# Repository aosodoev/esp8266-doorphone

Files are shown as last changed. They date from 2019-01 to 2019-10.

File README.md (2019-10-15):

# ESP8266 door phone w/ RFID lock

> If it looks stupid but works, it ain't stupid.

Crude door phone and RFID lock project for my yard gates door.

Handset unit serves as WiFi gateway/extender creating soft AP for door unit and connecting to existing WiFi network and MQTT broker.

Basic keys management and lock control via home assistant.

Using [PlatformIO](https://platformio.org) environment for development.

## Configuration
Create AP_credentials.h file in src dir (see doorphone.h for definitions). 

Edit mqtt_server param (without .local suffix) in settings.txt.

MQTT brocker IP address resolved via ESP8266mDNS library and requires MQTT service to be advertised.

e.g. mosquitto avahi service config: 

/etc/avahi/services/mosquitto.service
```
<!DOCTYPE service-group SYSTEM "avahi-service.dtd">
<service-group>
 <name replace-wildcards="yes">Mosquitto on %h</name>
  <service>
   <type>_mqtt._tcp</type>
   <port>1883</port>
   <txt-record>More info at mqtt.org</txt-record>
  </service>
</service-group>
```

## Hardware

As this is one time build, it's based on breakout boards/modules from ebay/aliexpress soldered to a perfboard.

Power door lock actuator unlocks a simple door bolt. Reed switch and a magnet used as door contact switch.

Initially it was very simple lock controller with one "open" button. Door phone and RFID reader were added later.

Audio quality turned out to be pretty good. There is no feedback noise due to earphone on the handset side. To get rid of digital noise and echo use shielded cable for microphone signal.

### Breakout boards/modules

MFRC522 reader missing here, any RC522 with SPI interface should work.

MCP3021 or TLC549 ADC can be used, add "ADC8BIT" define to build flags in case of TLC549 (see platformio.ini).

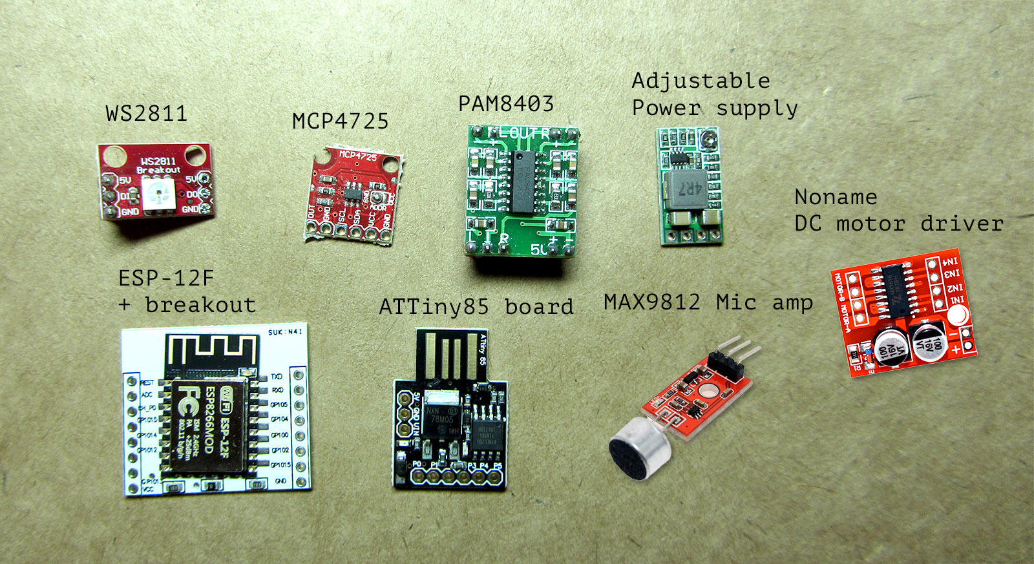
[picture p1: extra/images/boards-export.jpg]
Breakout boards


### Schematics

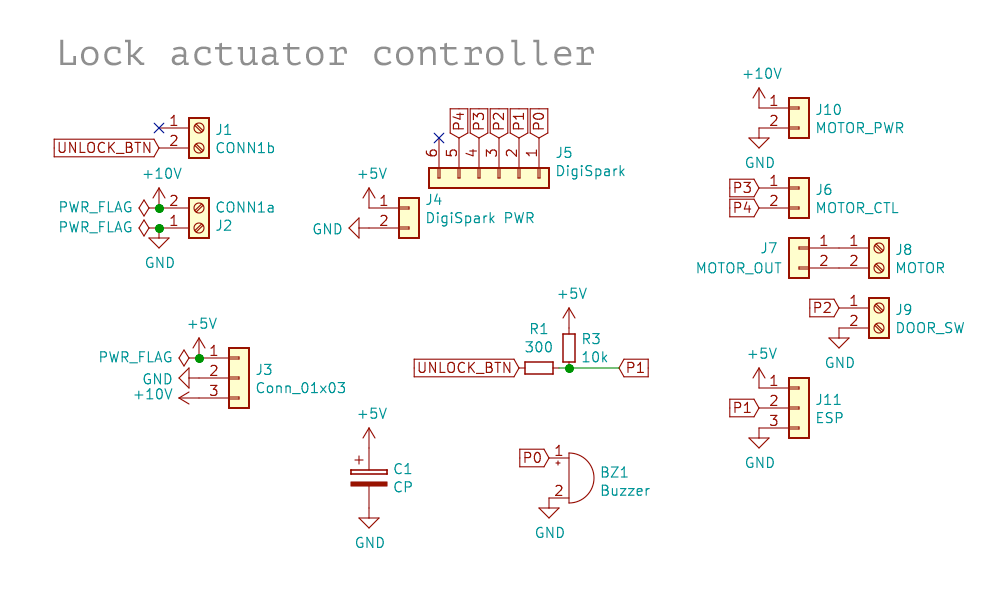
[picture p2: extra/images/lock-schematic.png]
Lock controller schematic


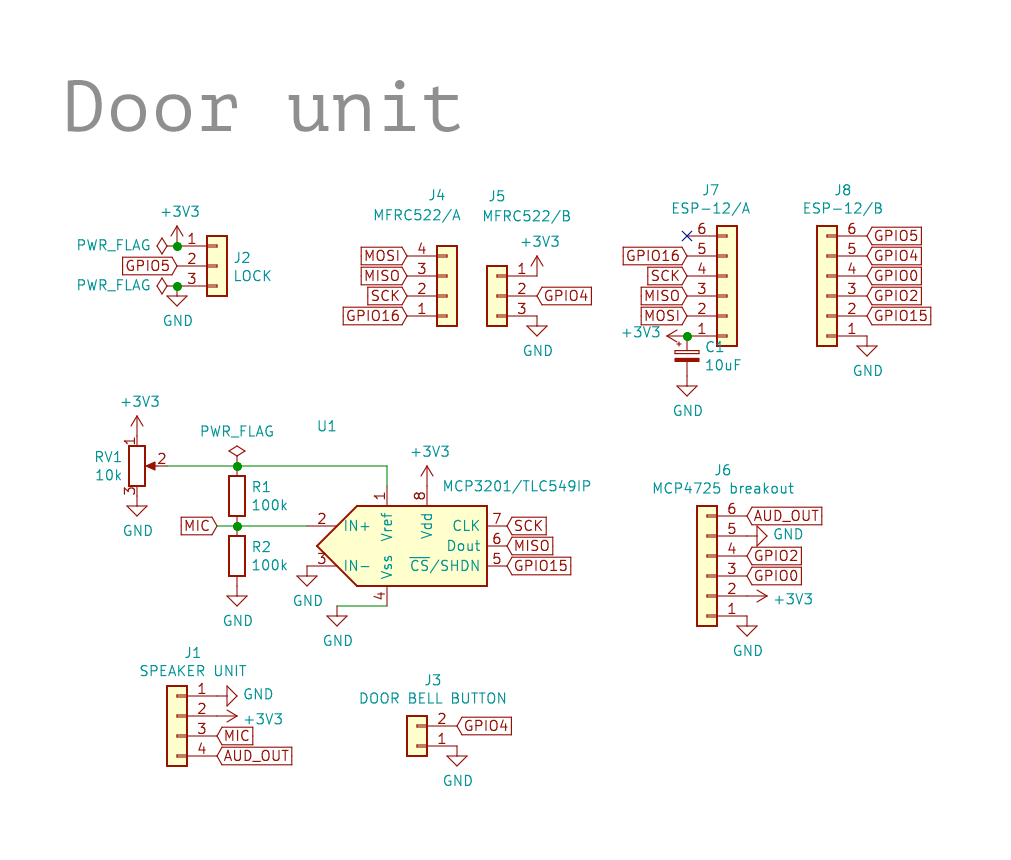
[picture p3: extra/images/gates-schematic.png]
Door unit schematic


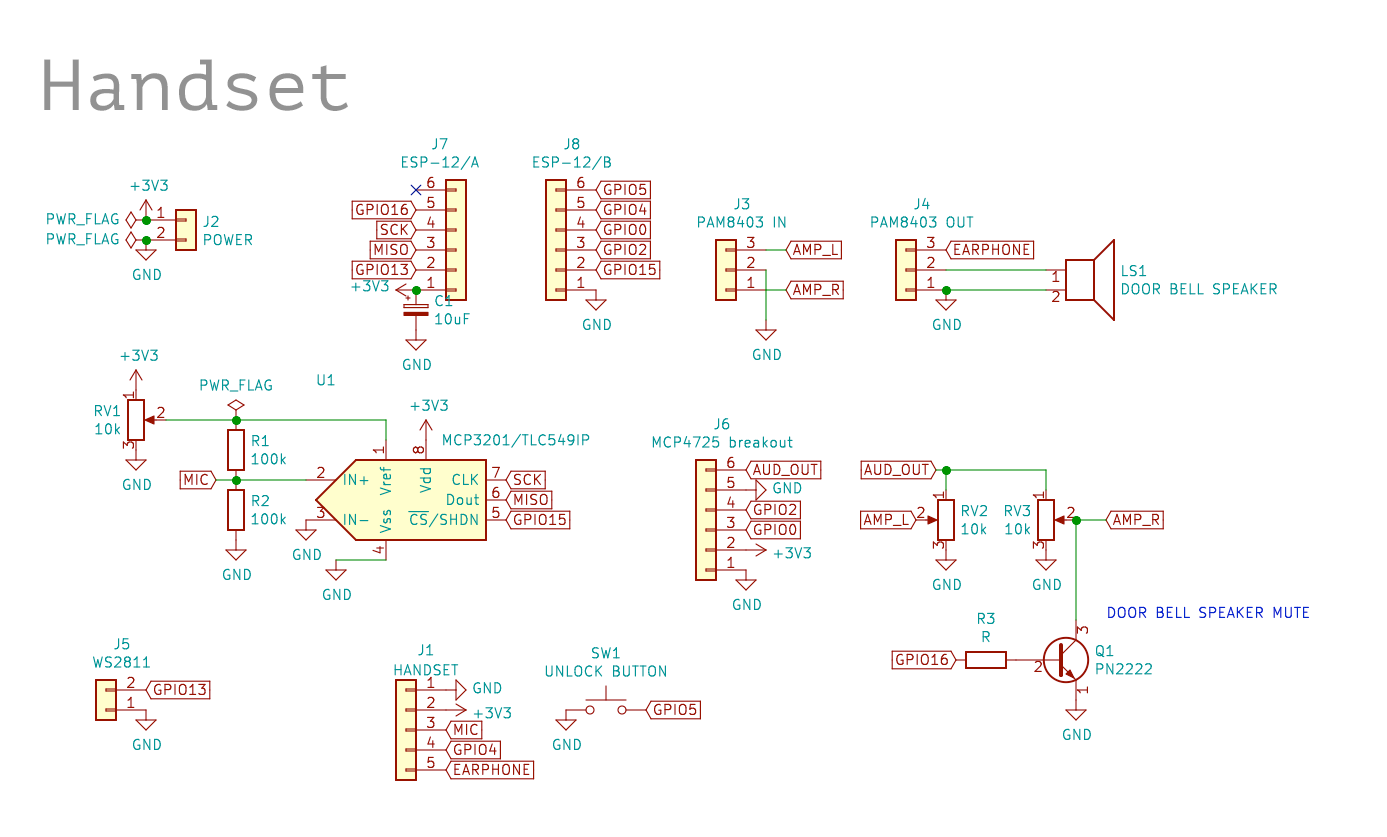
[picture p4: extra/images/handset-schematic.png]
Handset unit schematic


# WARNING
This implementation of RFID access control isn't even remotely secure and should not be used in any critical situation!

## Audio sources from freesound.org:

- Success: [https://freesound.org/people/grunz/sounds/109662/](https://freesound.org/people/grunz/sounds/109662/)

- Error: [https://freesound.org/people/Breviceps/sounds/445978/](https://freesound.org/people/Breviceps/sounds/445978/)

- "Door bell": [https://freesound.org/people/pac007/sounds/331567/](https://freesound.org/people/pac007/sounds/331567/)

- "Chirp": [https://freesound.org/people/IFartInUrGeneralDirection/sounds/96195/](https://freesound.org/people/IFartInUrGeneralDirection/sounds/96195/)

- "Electronic chirp": [https://freesound.org/people/organicmanpl/sounds/386973/](https://freesound.org/people/organicmanpl/sounds/386973/)

- "Echo": [https://freesound.org/people/Thoribass/sounds/254819/](https://freesound.org/people/Thoribass/sounds/254819/)

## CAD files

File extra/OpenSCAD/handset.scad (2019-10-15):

include<fillets.scad>
include<MCAD/units.scad>
use<MCAD/boxes.scad>
use<scad-utils/morphology.scad>
use<scad-utils/mirror.scad>

e = epsilon;
fitting_tolerance = 0.2;
boards_tolerance = 0.2;

shell_thickness = 1.6;
front_panel_thickness = 2;
inner_width = 46;
inner_height = 150;
inner_depth = 15;
inner_radius = 3;
outer_back_radius = 7.6;
front_cover_brim_depth = 4;

esp_board_width = 32;
esp_board_height = 28;
esp_board_thickness = 5.6;

speaker_radius = 14.9/2;
speaker_brim_height = 2.2;

mic_board_height = 14.1;
mic_radius = 9.6/2;
mic_height = 6.5;

ringtone_amp_height = 17.3;
ringtone_amp_width = 25.1;

outer_width = inner_width + 2*(shell_thickness + fitting_tolerance);
outer_height = inner_height + 2*(shell_thickness + fitting_tolerance);
outer_depth = inner_depth + front_panel_thickness + 2*shell_thickness;
outer_radius = inner_radius + shell_thickness + fitting_tolerance;


view = "explode";

if (view == "explode") {
     translate([0, 0, outer_depth - front_panel_thickness + 20]) {
	  rotate([0, 180, 0]) {
	       front_cover();
	  }
     }
     translate([0, 0, outer_depth - front_panel_thickness + 40]) {
	  %color([0.5, 0.5, 0.8, 0.5]) {
	       front_panel();
	  }
     }
     %color([0.5, 0.8, 0.5, 0.5]) {
	  back_cover();
     }
} else if (view == "handset-front-cover") {
     front_cover();
} else if (view == "handset-back-cover") {
     back_cover();
} else if (view == "handset-front-panel") {
     front_panel();
} else if (view == "handset-stand") {
     stand();
}

* union() {

    // test mic mount
    * test([20, 14, outer_height], 2) {
        front_cover();
    }

    // test speaker mount
    *test([20, 20, 7], inner_height - inner_width/2 - 10) {
        front_cover();
    }

    // test usb and reed switch
    * test([20, 26, 10], -3) {
        back_cover();
    }


    * test([inner_width, inner_width - 2, inner_depth], 90 - inner_width/2) {
	 back_cover();
    }

    // test button 
    * union() {
        button(negative = "top");
        test([30, 35, outer_height], inner_height/2 - 28) { front_cover(); }
    }
}


function x(v) = v[0]; function y(v) = v[1]; function z(v) = v[2];

module stand() {
     stand_size = [outer_width + 2*14, 80, 50];
     handset_angle = 12;
     handset_offset = y(stand_size) - outer_depth - 8;
     cutout_width = outer_width + 4;
     cutout_height = outer_depth + 1 + 4;

     difference() {
	  intersection() {
	       linear_extrude(z(stand_size)) {
		    rounding(10, $fn = 64) {
			 square(stand_size + [0, y(stand_size)], center = true);			 
		    }
	       }
	       rotate([0, -90, 0]) {
		    linear_extrude(x(stand_size) + 2*e, center = true) {
			 polygon([
				      [0, 0],
				      [z(stand_size), 0],
				      [15, y(stand_size)],
				      [0, y(stand_size)]

					   ]);
		    }
	       }
	  }

	  translate([0, handset_offset, 0]) {
	       rotate([handset_angle, 0, 0]) {
		    translate([0, 0, 3/cos(handset_angle)]) {
			 linear_extrude(outer_height) {
			      intersection() {
				   translate([0, cutout_height]) {
					rounding(outer_back_radius + 1, $fn = 32) {
					     square([cutout_width, cutout_height*2], center = true);
					}
				   }
				   square([cutout_width, cutout_height*2], center = true);
			      }
			 }
		    }
	       }
	  }

	  translate([0, -e, -e]) {
	       intersection() {
		    rotate([-90 - 20, 0, 0]) {
			 linear_extrude(y(stand_size)*2, center = true) {
			      rounding(20-e, $fn = 64) {
				   square([40, 2*z(stand_size) - 15], center = true);
			      }
			 }
		    }
		    rotate([0, -90, 0]) {
			 linear_extrude(x(stand_size), center = true) {
			      polygon([
					   [0, 0],
					   [z(stand_size), 0],
					   [z(stand_size), handset_offset - 1.6/cos(handset_angle) - z(stand_size)*tan(handset_angle)],
					   [0, handset_offset - 2]
					   
					   ]);
			 }
		    }
	       }
	  }
	  translate([0, y(stand_size), -e]) {
	       linear_extrude(z(stand_size)) {
		    rounding(6, $fn = 16) {
			 square([cutout_width - 6*2, (y(stand_size) - handset_offset - 6) * 2], center = true);
		    }
	       }
	  }
	  mirror_x() {
	       rotate([-90, 0, 0]) {
		    translate([(x(stand_size) + 40)/4, -z(stand_size) + 18, -e]) {
			 translate([-6, -14, 3]) {
			      cube([12, 20, 4]);
			 }
			 cylinder(4, r = 4);
			 hull() {
			      cylinder(4, r = 2);
			      translate([0, -8, 0]) {
				   cylinder(4, r = 2);
			      }
			 }
		    }
	       }
	  }
     }

     reed_switch_position = 15 + 2 + shell_thickness;
     magnet_radius = 14.6/2;
     magnet_height = 3;

     translate([0, handset_offset - 1.6/cos(handset_angle), 0]) {
	  rotate([handset_angle, 0, 0]) {
	       translate([0, 0, reed_switch_position + 3/cos(handset_angle)]) {
		    rotate([90, 0, 0]) {
			 difference() {
			      hull() {
				   cylinder(6, r = magnet_radius + fitting_tolerance + 2);
				   translate([0, -6*1.2, 0]) {
					cylinder(e, r = magnet_radius + fitting_tolerance + 2);
				   }
			      }
			      difference() {
				   cylinder(6 + e, r = magnet_radius + fitting_tolerance, $fn = 64);
				   mirror_x(){
					mirror_y() {
					     translate([(magnet_radius + fitting_tolerance)*cos(45), (magnet_radius + fitting_tolerance)*cos(45), magnet_height + 0.4]) {
						  sphere(0.4, $fn = 64);
					     }
					}
				   }					
			      }
			 }
		    }
	       }
	  }
     }

     	  *translate([0, handset_offset, 0]) {
	       rotate([handset_angle, 0, 0]) {
		    translate([0, 0, 3/cos(handset_angle)]) {
			 color([0, 1, 0, 0.3]) {
			      linear_extrude(outer_height) {
				   intersection() {
					translate([0, outer_depth + 1]) {
					     rounding(outer_back_radius, $fn = 32) {
						  square([outer_width, outer_depth*2 + 1], center = true);
					     }
					}
					square([outer_width, outer_depth*2 + 1], center = true);
				   }
			      }
			 }
		    }
	       }
	  }

     
}
    
module front_panel() {

     front_panel_thickness = front_panel_thickness + 1;
     
     difference() {
	  union() {
	       translate([0, inner_height/2, 0]) {
		    linear_extrude(front_panel_thickness) {
                        rounding(r = inner_radius, $fn = 32) {
                            square([inner_width, inner_height], center = true);
                        }
                    }
	       }
	       front_panel_latches(negative = false);

	       translate([0, inner_height - inner_width/2 - fitting_tolerance, 0]) {
		    /* speaker(); */
	       }
            
	       // mic cutout
	       translate([0, shell_thickness + mic_board_height/2 + boards_tolerance, 0]) {
		    /* microphone(); */
	       }
            
	       
	  } // main union

	  // cut outs

	  translate([0, inner_height - inner_width/2 - fitting_tolerance, -e]) {
	       mirror_y() {
		    hull() {
			 mirror_x() {
			      translate([5, 2, 0]) {
				   cylinder(front_panel_thickness + 2*e, r = 1, top = 0.8, bottom = 0, $fn = 16, fillet_fn = 16);
			      }
			 }
		    }
	       }
	       /* speaker(); */
	  }
	  
	  // mic cutout
	  translate([0, shell_thickness + mic_board_height/2 + boards_tolerance, -e]) {
	       cylinder(front_panel_thickness + e*2, r = 1.25, $fn = 16);
	       /* microphone(); */
	  }
	  
	  // button cutout
	  translate([0, inner_height / 2 - 5, -e]) {
	       cylinder_fillet_outside(front_panel_thickness + e*2, r = 6 + 0.5, top = 0.8, bottom = 0, $fn = 64, fillet_fn = 64);
	  }
	  
	  
     } // main difference

     // button
     translate([0, inner_height / 2 - 5, 0]) {
	  difference() {
	       cylinder_fillet_inside(front_panel_thickness, r = 6, top = 0.5, bottom = 0, $fn = 128, fillet_fn = 64);
	       sphere_r  = 20;
	       translate([0, 0, front_panel_thickness + sphere_r - 0.76]) {
		    sphere(sphere_r, $fn = 256);
	       }
	  }
     }

}

module front_panel_latches(negative = false) {
     mirror_x() {
	  for (pos = [20, inner_height/2, inner_height - 20]) {
	       translate([inner_width/2 + (negative ? fitting_tolerance : 0), pos, 0.6 + (negative ? outer_depth - front_panel_thickness : 0)]) {
		    rotate([90, 0, 0]) {
			 cylinder(8 + (negative ? fitting_tolerance*2 : 0), r = 0.6 + (negative ? fitting_tolerance : 0), $fn = 10, center = true);
		    }
	       }
	  }
     }
}
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

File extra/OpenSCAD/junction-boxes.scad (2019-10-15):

include<MCAD/units.scad>
include<MCAD/boxes.scad>
include<fillets.scad>
include<scad-utils/morphology.scad>
include<scad-utils/mirror.scad>

e = epsilon;
fitting_tolerance = 0.1;

tube_diameter = 13;


     inner_size = [26, 50, 25];
    
     base_thickness = 3;
     thickness = 1.6;
     outer_radius = 5;
     inner_radius = outer_radius - thickness;

     cover_depth = 5;


if (false) {
// door_magnet();
     reed_switch_box();
     translate ([50, 0, 0]) {
	  reed_switch_box_cover();
     }
} else {
     power_box();
     translate ([50, 0, 0]) {
	  power_box_cover();
     }
     
}

module door_magnet() {
     magnet_size = [15, 12, 8.3];
     difference() {
	  minkowski() {
	       translate([0, 0, magnet_size[2]/2]) {
		    cube(magnet_size + [2*10, 0, 0], center = true);
	       }
	       sphere(r = 1.6 + fitting_tolerance, $fn = 64);
	  }
	  translate([0, 0, magnet_size[2]/2 + fitting_tolerance - e]) {
	       cube(magnet_size + [fitting_tolerance, fitting_tolerance, fitting_tolerance]*2, center = true);
	  }
	  translate([-20, -10, -2]) {
	       cube([40, 20, 2]);
	  }
	  mirror_x() {
	       total_height = magnet_size[2] + 1.6 + fitting_tolerance;
	       translate([magnet_size[0]/2 + 6, 0, -e]) {
		    cylinder(total_height + e*2, r = 2, $fn = 32);
		    translate([0, 0, total_height - 2]) {
			 cylinder(2 + 2*e, r1 = 2, r2 = 4, $fn = 32);
		    }
	       }
	  }
     }
     mirror_y() {
	  translate([0, magnet_size[1]/2 + fitting_tolerance + 0.15, 2]) {
	       rotate([0, 90, 0]) {
		    cylinder(5, r = 0.3, center = true, $fn = 20);
	       }
	  }
     }
}


module reed_switch_box() {
     difference() {
	  union() {
	       linear_extrude(inner_size[2] + base_thickness - cover_depth) {
		    rounding(outer_radius, $fn = 64) {
			 square(inner_size + [thickness, thickness]*2, center = true);
		    }
	       }
	       translate([0, 0, inner_size[2] + base_thickness - cover_depth - e]) {
		    linear_extrude(cover_depth + e) {
			 rounding(inner_radius, $fn = 64) {
			      square(inner_size + [0, 0], center = true);
			 }
		    }
	       }
	       translate([0, 0, inner_size[2] + base_thickness - cover_depth/2]) {
		    minkowski() {
			 linear_extrude(e) {
			      rounding(inner_radius - 0.2, $fn = 64) {
				   square(inner_size - [0.2, 0.2]*2, center = true);
			      }
			 }
			 sphere(r = 0.4, $fn = 20);
		    }
	       }

	  }
	  translate([0, 0, base_thickness]) {
	       hull() {
		    linear_extrude(inner_size[2] - cover_depth - 3*thickness) {
			 rounding(inner_radius, $fn = 32) {
			      square(inner_size + [0, 0], center = true);
			 }
		    }
		    translate([0, 0, inner_size[2] - cover_depth]) {
			 linear_extrude(e) {
			      rounding(inner_radius - thickness, $fn = 32) {
				   square(inner_size - [thickness, thickness]*2, center = true);
			      }
			 }
		    }
	       }
	       translate([0, 0, inner_size[2] - cover_depth]) {
		    linear_extrude(cover_depth + e) {
			 rounding(inner_radius - thickness, $fn = 32) {
			      square(inner_size - [thickness, thickness]*2, center = true);
			 }
		    }
	       }
	  }
	  translate([0, -inner_size[1]/2 - thickness - e, (inner_size[2] + base_thickness + thickness)/2]) {
	       rotate([-90, 0, 0]) {
		    hull() {
			 for (pos = [0, -50]) {
			      translate([0, pos, 0]) {
				   cylinder(2*thickness + 2*e, r = tube_diameter/2);
			      }
			 }
		    }
		    hull() {
			 for (pos = [0, -50]) {
			      translate([0, pos, 0]) {
				   translate([0, 0, -1]) {
					cylinder(thickness + 2*e, r = 16.5/2);
				   }

			      }
			 }
		    }
	       }
	  }
	  mirror_x() {
	       mirror_y() {
		    union() {
		    translate([inner_size[0]/2 - 5, inner_size[1]/2 - 5, base_thickness - 1]) {
			 cylinder(1 + e, r1 = 1.7, r2 = 3, $fn = 16);
		    }
		    translate([inner_size[0]/2 - 5, inner_size[1]/2 - 5, -e]) {
			 cylinder(base_thickness + 2*e, r = 1.7, $fn = 16);
		    }
		    }
	       }
	  }
	  translate([inner_size[0]/2 - 5, -inner_size[1]/2 - thickness - e, base_thickness + 4]) {
	       rotate([-90, 0, 0]) {
		    cylinder(2*thickness + 2*e, r = 2, $fn = 12);
	       }
	  }

     }
     reed_width = 2.6 + 2*fitting_tolerance;
     mirror_y() {
	  translate([-inner_size[0]/2, 7 - 2, base_thickness + inner_size[2]/2]) {
	       rotate([90, 0, 0]) {
		    linear_extrude(4, center = true) {
			 polygon([[-e, 0], [reed_width, 0], [reed_width, reed_width], [reed_width - 0.4, reed_width + 0.4], [reed_width, reed_width + 0.4*3], [reed_width + 1.2, reed_width + 0.4*3], [reed_width + 1.2, -reed_width], [-e, -reed_width*3]]);
		    }
	       }
	  }
     }
}

module reed_switch_box_cover() {
     
     difference() {
	  union() {
	       linear_extrude(cover_depth + thickness) {
		    rounding(outer_radius, $fn = 64) {
			 square(inner_size + [thickness, thickness]*2, center = true);
		    }
	       }
	       translate([-tube_diameter/2 + 0.5, -inner_size[1]/2 - thickness, 0]) {
		    cube([tube_diameter - 0.5*2, thickness, inner_size[2]/2]);
	       }
	  }
	  translate([0, 0, thickness]) {
	       linear_extrude(cover_depth + e) {
		    rounding(inner_radius + fitting_tolerance, $fn = 32) {
			 square(inner_size + [fitting_tolerance, fitting_tolerance]*2, center = true);
		    }
	       }
	  }
	  translate([0, 0, thickness + cover_depth/2]) {
	       minkowski() {
		    linear_extrude(e) {
			 rounding(inner_radius - 0.2, $fn = 64) {
			      square(inner_size - [0.2, 0.2]*2, center = true);
			 }
		    }
		    sphere(r = 0.5, $fn = 20);
	       }
	  }
	  translate([0, -inner_size[1]/2 - thickness - e, (inner_size[2] + base_thickness + thickness)/2]) {
	       rotate([-90, 0, 0]) {
		    cylinder(2*thickness + 2*e, r = tube_diameter/2);
		    translate([0, 0, -1]) {
			 cylinder(thickness + 2*e, r = 16.5/2);
		    }
	       }
	  }
     }
}

module power_box() {

     inner_size = [35, 45, 20];
    
     base_thickness = 3;
     thickness = 1.6;
     outer_radius = 5;
     inner_radius = outer_radius - thickness;

     cover_depth = 5;

     tube_diameter = 12;
     
     difference() {
	  union() {
	       linear_extrude(inner_size[2] + base_thickness - cover_depth) {
		    rounding(outer_radius, $fn = 64) {
			 square(inner_size + [thickness, thickness]*2, center = true);
		    }
	       }
	       translate([0, 0, inner_size[2] + base_thickness - cover_depth - e]) {
		    linear_extrude(cover_depth + e) {
			 rounding(inner_radius, $fn = 64) {
			      square(inner_size + [0, 0], center = true);
			 }
		    }
	       }
	       translate([0, 0, inner_size[2] + base_thickness - cover_depth/2]) {
		    minkowski() {
			 linear_extrude(e) {
			      rounding(inner_radius - 0.2, $fn = 64) {
				   square(inner_size - [0.2, 0.2]*2, center = true);
			      }
			 }
			 sphere(r = 0.5, $fn = 20);
		    }
	       }

	  }
	  translate([0, 0, base_thickness]) {
	       hull() {
		    linear_extrude(inner_size[2] - cover_depth - 3*thickness) {
			 rounding(inner_radius, $fn = 32) {
			      square(inner_size + [0, 0], center = true);
			 }
		    }
		    translate([0, 0, inner_size[2] - cover_depth]) {
			 linear_extrude(e) {
			      rounding(inner_radius - thickness, $fn = 32) {
				   square(inner_size - [thickness, thickness]*2, center = true);
			      }
			 }
		    }
	       }
	       translate([0, 0, inner_size[2] - cover_depth]) {
		    linear_extrude(cover_depth + e) {
			 rounding(inner_radius - thickness, $fn = 32) {
			      square(inner_size - [thickness, thickness]*2, center = true);
			 }
		    }
	       }
	  }
	  translate([-4, -inner_size[1]/2 - thickness - e, (inner_size[2] + thickness)/2]) {
	       rotate([-90, 0, 0]) {
		    cylinder(2*thickness + 2*e, r = tube_diameter/2);
	       }
	  }
	  mirror_x() {
	       mirror_y() {
		    union() {
		    translate([inner_size[0]/2 - 5, inner_size[1]/2 - 5, base_thickness - 1]) {
			 cylinder(1 + e, r1 = 1.7, r2 = 3, $fn = 16);
		    }
		    translate([inner_size[0]/2 - 5, inner_size[1]/2 - 5, -e]) {
			 cylinder(base_thickness + 2*e, r = 1.7, $fn = 16);
		    }
		    }
	       }
	  }
	  translate([inner_size[0]/2 - 9, -inner_size[1]/2 - thickness - e, base_thickness + 4]) {
	       rotate([-90, 0, 0]) {
		    cylinder(2*thickness + 2*e, r = 2, $fn = 12);
	       }
	  }

     }
}

module power_box_cover() {

     inner_size = [35, 45, 20];
    
     base_thickness = 3;
     thickness = 1.6;
     outer_radius = 5;
     inner_radius = outer_radius - thickness;
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

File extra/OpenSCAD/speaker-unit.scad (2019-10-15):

include<MCAD/units.scad>
use<fillets.scad>
use<scad-utils/morphology.scad>

e = epsilon;

speaker_radius = 40/2;
speaker_brim_height = 1.5;

mic_board_height = 14.1;
mic_radius = 9.6/2;
mic_height = 6.5;

connector_width = 12;
connector_height = 7;

mfrc_width = 60;
mfrc_height = 40;

main_board_height = 25;
main_board_width = 30;

boards_tolerance = 0.4;
fitting_tolerance = 0.2;

shell_thickness = 1.6;
front_panel_thickness = 2;

inner_width = mfrc_width + 2*boards_tolerance;
outer_width = inner_width + 2*shell_thickness;

inner_height = 170;
outer_height = inner_height + 2*shell_thickness;

inner_depth = 15;
outer_depth = inner_depth + shell_thickness; // only front shell will add up

outer_radius = 3;
inner_radius = outer_radius - shell_thickness;


amp_pos = inner_height - inner_width - 14;
mfrc_pos = amp_pos - 1.2 - (mfrc_height + 2*boards_tolerance);
main_board_pos = mfrc_pos - 1.2 - (main_board_height + 2*boards_tolerance);

view = "explode";

if (view == "explode") {
     translate([0, 0, shell_thickness + 20]) {
	  %color([0.6, 0.3, 0, 0.5]) {
	       back_cover();
	  }
     }
     %color([0.6, 0.3, 0, 0.5]) {
	  back_cover_brim();
     }
     translate([0, 0, 80]) {
	  rotate([0, 180, 0]) {	       
	       main_shell();
	  }
     }
     translate([0, 0, 100]) {
	  color([0.6, 0.3, 0, 0.3]) {
	       render() {
		    front_panel();
	       }
	  }
     }
} else if (view == "speaker-front-cover") {
     main_shell();
} else if (view == "speaker-back-cover") {
     back_cover();
} else if (view == "speaker-brim") {
     back_cover_brim();
} else if (view == "speaker-front-panel") {
     front_panel();
}


// tests
* intersection () {
    back_cover();
    * translate([-outer_width/2, -shell_thickness, 0]) {
        // mic and cable thingy
        cube([outer_width, 27, outer_depth + 2]);
        // main board
        translate([0, main_board_pos + main_board_height/2 - 4, 0])
            cube([outer_width, 12, outer_depth + 2]);
        
        translate([0, mfrc_pos + mfrc_height/2 - 4, 0])
            cube([outer_width, 12, outer_depth + 2]);
    }
}
* intersection() {
    main_shell();
    mirror([1, 0, 0]) {
        translate([0, -5, 0])
        cube([outer_width, outer_height + 8, outer_depth + 20]);
    }
}

module front_panel() {

     speaker_grill_width = inner_width - 8;
     speaker_grill_height = (speaker_radius + 5) * 2 + 6;
     
     difference() {
	  union() {
	       translate([0, outer_height/2 - shell_thickness, 0]) {
		    linear_extrude(front_panel_thickness) {
			 rounding(outer_radius, $fn = 64) {
			      square([outer_width, outer_height], center = true);

			 }
		    }
		    linear_extrude(front_panel_thickness + 2) {
			 shell(d = -3) {
			      rounding(outer_radius, $fn = 64) {
				   square([outer_width, outer_height], center = true);
			      }
			 }
		    }
	       }
	               
	       // button
	       translate([-5 - 6 - shell_thickness, mfrc_pos - 20 + 7 + shell_thickness, 0]) {
		    cylinder(3, r = 6 + 1.6 + fitting_tolerance, $fn = 64);
		    translate([17, -4, 0]) {
			 rotate([0, 0, -10]) {
			      linear_extrude(2 + 0.6) {
				   outset(d=0.3) {
					text("%", font = "Wingdings:style=Bold", size = 12);
				   }
			      }
			 }
		    }
	       }

	       translate([0, mfrc_pos - 20 + 6 + shell_thickness, 0]) {
		    linear_extrude(3) {
			 shell(d = -2) {
			      rounding(4, $fn = 32) {
				   square([speaker_grill_width, (6 + shell_thickness + fitting_tolerance + 2 + 4) * 2], center = true);
			      }
			 }
		    }
	       }

	       translate([0, mfrc_pos + 28, 0]) {
		    linear_extrude(2.4) {
			 shell(d = -1) {
			      rounding(4, $fn = 32) {
				   square([speaker_grill_width, 40], center = true);
			      }
			 }
		    }		    
	       }

	  } // union

	  // speaker compartment
	  translate([0, inner_height - inner_width/2 - fitting_tolerance - 4, -e]) {
	       linear_extrude(3 + 2*e) {
		    inset(d = 2) {
			 rounding(4, $fn = 64) {
			      square([speaker_grill_width, speaker_grill_height], center = true);
			 }
		    }
	       }

	  }

	  // button cutout
	  translate([-5 - 6 - shell_thickness, mfrc_pos - 20 + 7 + shell_thickness, -e]) {
	       cylinder(3 + 2*e, r = 6 + fitting_tolerance, $fn = 64);
	  }

	  // mic cutout
	  translate([0, shell_thickness + mic_board_height/2 + boards_tolerance, 0]) {
	       translate([0, 0, 0.6/2]) {
		    cube([mic_board_height, mic_board_height, 0.6 + 2*e], center = true);
	       }
	       for (y = [-mic_board_height/2:1.2 + 1:mic_board_height/2 - 2]) {
		    translate([0, y, 0.6]) {
			 rotate([0, -90, 0]) {
			      linear_extrude(mic_board_height, center = true) {
				   polygon([
						[3 + e, -0.5],
						[3 + e, 0.5],
						[3 - 0.6, 0.5],
						[-e, 3 - 0.6 + 0.5],
						[-e, 3 - 0.6 - 0.5],
						[3 - 0.6, -0.5]
						]);
			      }
			 }
		    }
	       }
	  }

	  
     } // main difference

     // speaker
     translate([0, inner_height - inner_width/2 - fitting_tolerance - 4, 0]) {
	  
	  linear_extrude(3) {
	       shell(d = -2) {
		    rounding(4, $fn = 64) {
			 square([speaker_grill_width, speaker_grill_height], center = true);
		    }
	       }
	  }
	  difference() {
	       linear_extrude(3) {
		    inset(d = 3) {
			 rounding(4, $fn = 64) {
			      square([speaker_grill_width, speaker_grill_height], center = true);
			 }
		    }
	       }
	       for (y = [-speaker_grill_height/2 + 7:4:speaker_grill_height/2 - 6]) {
		    translate([0, y, 0]) {
			 rotate([0, -90, 0]) {
			      linear_extrude(inner_width, center = true) {
				   polygon([
						[3 + e, -0.5],
						[3 + e, 0.5],
						[3 - 0.6, 0.5],
						[-e, 3 - 0.6 + 0.5],
						[-e, 3 - 0.6 - 0.5],
						[3 - 0.6, -0.5]
						]);
			      }
			 }
		    }
	       }
	  }
	  linear_extrude(1.6) {
	       difference() {
		    inset(d = 3) {
			 rounding(4, $fn = 64) {
			      square([speaker_grill_width, speaker_grill_height], center = true);
			 }
		    }
		    translate([0, 4]) {
			 circle(r = speaker_radius - 2);
		    }
	       }
	  }

	  
     }

}
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

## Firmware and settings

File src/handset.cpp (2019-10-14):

#include <SPI.h>


// #define AUDIO_DEBUG

#ifndef DISABLE_STA
#include <ESP8266mDNS.h>
#include <WiFiManager.h>
#include <PubSubClient.h>
#endif

#ifdef ENABLE_WEB_GUI
#include <web-ui.h>
#include <ArduinoJSON.h>
#include <Ticker.h>
#endif

#include <ArduinoOTA.h>
#include <FS.h>

#include <Adafruit_NeoPixel.h>

#include "doorphone.h"
#include "audio.h"

#define SOFT_AP_HIDDEN true

#define CONNECT_BTN_PIN 4
#define UNLOCK_BTN_PIN 5
#define SPK_EN_PIN 16

#ifndef CONNECT_BTN_ACTIVE
#define CONNECT_BTN_ACTIVE LOW
#endif

#ifdef PT8211
#define LED_DATA_PIN 0
#else
#define LED_DATA_PIN 13
#endif

#define STATUS_LED 0
#define SPK_EN LOW

enum {MQTT_CMD_LOCK = 0, MQTT_CMD_KEYS_ADD, MQTT_CMD_KEYS_DELETE, MQTT_CMD_KEYS_LIST, MQTT_CMD_UNKNOWN};

struct {
#ifndef DISABLE_STA
  char mqtt_server[32] = "miniboxxy"; // mdns hostname in .local domain
#endif
  char ringtone[32] = "/bell.g722";
  uint8_t nkeys = 0;
  struct {
    uint8_t id[4];
    char comment[128];
    bool status;
  } keys[32];
} settings;

#ifdef DEBUG
char unknown_key[16] = "FF:FF:FF:FF";
#else
char unknown_key[16] = "";
#endif

Adafruit_NeoPixel leds = Adafruit_NeoPixel(1, LED_DATA_PIN, NEO_GRB + NEO_KHZ800);

WiFiUDP udp;

WiFiClient wlclient;

#ifndef DISABLE_STA
PubSubClient mqtt(wlclient);
#endif

IPAddress gatecontrol_ip = IPAddress(GATECONTROL_IP);
IPAddress handset_ip = IPAddress(HOUSTON_IP);

static struct {
  int retry;
  int repeat_timeout;
} outgoing_msgs[INTERCOM_MSG_NUM];


#ifdef AUDIO_DEBUG
int status = HANDSET_STATUS_IDLE;
#else
int status = HANDSET_STATUS_DISCONNECTED;
#endif

uint32_t status_color[] = {
  [HANDSET_STATUS_NONE] = 0,
  [HANDSET_STATUS_DISCONNECTED] = leds.Color(16, 0, 0),
  [HANDSET_STATUS_IDLE] = leds.Color(0, 16, 0),
  [HANDSET_STATUS_RINGING] = leds.Color(255, 0, 255),
  [HANDSET_STATUS_VOICE] = leds.Color(0, 128, 0),
  [HANDSET_STATUS_VOICE_MUTE] = leds.Color(0, 0, 128),
};

const char *mqtt_command[] =
  {
   [MQTT_CMD_LOCK] = "lock/set",
   [MQTT_CMD_KEYS_ADD] = "keys/add",
   [MQTT_CMD_KEYS_DELETE] = "keys/delete",
   [MQTT_CMD_KEYS_LIST] = "keys/list"
  };

unsigned long
  ringer_started = 0,
  ringer_repeat_timeout = 0,
  voice_started = 0,
  mqtt_unlock_published = 0;


/*
 * Load settings from settings.txt
 */
void readSettings() {
  File f;
  char *buf, *key, *value;
  
  f = SPIFFS.open("/settings.txt", "r");
  if (!f) {
    DPRINTF("Can't open settings file, module will use hardcoded fallback values.");
    return;
  }

  buf = new char[f.size() + 1];
  f.read((uint8_t *)buf, f.size());
  buf[f.size()] = '\0';
  f.close();

  DPRINTF("settings.txt:\n%s", buf);

  key = strtok(buf, "\n\r");

  settings.nkeys = 0;
  
  while (key) {
    value = strchr(key, '=');
    if (value) {
      *value = '\0'; value++;
      if (strcmp(key, "key") == 0) {
	int id_int[4];
	if (sscanf(value, "%x:%x:%x:%x;%s",
		   &id_int[0], &id_int[1], &id_int[2], &id_int[3], settings.keys[settings.nkeys].comment) == 5) {
	  for (int i=0; i<4; i++) {
	    settings.keys[settings.nkeys].id[i] = id_int[i];
	  }
	  settings.keys[settings.nkeys++].status = true;
	}
#ifndef DISABLE_STA
      } else if (strcmp(key, "mqtt_server") == 0) {
        strcpy(settings.mqtt_server, value);
#endif	
      } else if (strcmp(key, "ringtone") == 0) {
	strcpy(settings.ringtone, value);
      }
    }
    key = strtok(NULL, "\n\r");
  }

  delete [] buf;
  buf = NULL;
}

void saveSettings() {
  File f;
    
  f = SPIFFS.open("/settings.txt", "w");
  if (!f) {
    DPRINTF("Can't open settings.txt.");
    return;
  }
  
#ifndef DISABLE_STA  
  f.printf("mqtt_server=%s\n", settings.mqtt_server);
#endif
  
  f.printf("ringtone=%s\n", settings.ringtone);

  for (int i = 0; i < settings.nkeys; i++) {
    if (settings.keys[i].status) {
      f.printf("key=%X:%X:%X:%X;%s\n",
	       settings.keys[i].id[0],
	       settings.keys[i].id[1],
	       settings.keys[i].id[2],
	       settings.keys[i].id[3],
	       settings.keys[i].comment);
    }
  }
  DPRINTF("Current settings saved to settings.txt");
  
}


#ifndef DISABLE_STA
IPAddress mdns_resolve(const char hostname[], const char service[], const char protocol[]) {
  int n = MDNS.queryService(service, protocol);
  for (int i = 0; i < n; i++) {
    if (MDNS.hostname(i) == hostname) {
      return MDNS.IP(i);
    }
  }
  return IPAddress();
}

void mqtt_reconnect() {

  // Wait 5 seconds before trying again
  static unsigned long previous_attempt = 0;
  if (millis() - previous_attempt < 5000) {
    return;
  }  
  previous_attempt = millis();

  IPAddress mqtt_ip = mdns_resolve(settings.mqtt_server, "mqtt", "tcp");
  
  if (!mqtt_ip) {
    DPRINTF("\"%s.local\" not found", settings.mqtt_server);
    return;
  } else {
    DPRINTF("Found \"%s.local\": %d.%d.%d.%d", settings.mqtt_server, mqtt_ip[0], mqtt_ip[1],mqtt_ip[2],mqtt_ip[3]);
    mqtt.setServer(mqtt_ip, 1883);
  }

  if (mqtt.connect("gatescontrol")) {
    DPRINTF("Connected to MQTT broker");
    mqtt.subscribe("yard/gates/lock/set", 1); // 1 - QOS - "at least once"
    mqtt.subscribe("yard/gates/keys/+", 1);
    mqtt.publish("yard/gates/status", "ONLINE");
    mqtt.publish("yard/gates/lock/status", "LOCK", true);
  } else {
    DPRINTF("Connection to MQTT broker failed, rc=");
  }
}

void mqtt_callback(const char topic[], byte* payload, unsigned int length);

#endif


void bell_begin() {
  ringer_repeat_timeout = 0;
  ringer_started = millis();
  digitalWrite(SPK_EN_PIN, SPK_EN);
  status = HANDSET_STATUS_RINGING;
}

void bell_end() {
  audio_streaming_end();
  digitalWrite(SPK_EN_PIN, !SPK_EN);
  ringer_started = 0;
  if (status == HANDSET_STATUS_RINGING)
    status = HANDSET_STATUS_IDLE;
}

void voice_begin(bool mute = false) {
  DPRINTF("Voice communication begin.");
  bell_end();
  audio_streaming_begin(UDPSTREAM);
  // audio_streaming_begin("/success.g722");
  status = HANDSET_STATUS_VOICE_MUTE;
  if (!mute) {
    audio_sampling_begin(gatecontrol_ip);
    status = HANDSET_STATUS_VOICE;
  }
  voice_started = millis();
}

void voice_end() {
  audio_sampling_end();
  audio_streaming_end();
  // audio_streaming_begin("/hangup.g722");
  voice_started = 0;
  if (status == HANDSET_STATUS_VOICE || status == HANDSET_STATUS_VOICE_MUTE)
    status = HANDSET_STATUS_IDLE;
  
  DPRINTF("Voice communication end.");
}

int key_index(uint8_t id[4]) {
  for (int i = 0; i < settings.nkeys; i++) {
    if (memcmp(settings.keys[i].id, id, 4) == 0)
      return i;
  }
  return -1;
}

bool add_key(const char *key) {
  uint8_t id[4];
  int id_int[4];
  if (sscanf(key, "%x:%x:%x:%x;%s",
	     &id_int[0], &id_int[1], &id_int[2], &id_int[3], settings.keys[settings.nkeys].comment) == 5) {
    for (int i=0; i<4; i++) {
      id[i] = id_int[i];
    }
    DPRINTF("New key: %s, unknown key: %s, length: %d", key, unknown_key, strchr(key, ';') - key);
    if (key_index(id) != -1) {
      DPRINTF("Key already known.");
    } else {
      if (strncmp(unknown_key, key, strchr(key, ';') - key) == 0) {
	unknown_key[0] = 0;
      }
      memcpy(settings.keys[settings.nkeys].id, id, 4);
      settings.keys[settings.nkeys++].status = true;
      DPRINTF("Added key: %02X:%02X:%02X:%02X", id_int[0], id_int[1], id_int[2], id_int[3]);
      saveSettings();
      outgoing_msgs[INTERCOM_MSG_KEYRING].retry = MSG_RETRY_COUNT;
      return true;
    }
  } else {
    DPRINTF("Error parsing key.");
  }
  return false;
}

bool delete_key(const char *key) {
  int index;
  uint8_t id[4];
  int id_int[4]; 
  if (sscanf(key, "%x:%x:%x:%x",
	     &id_int[0], &id_int[1], &id_int[2], &id_int[3]) == 4) {
    for (int i=0; i<4; i++) {
      id[i] = id_int[i];
    }
    index = key_index(id);
    if (index != -1) {
      settings.keys[index].status = false;
      saveSettings();
      readSettings();
      outgoing_msgs[INTERCOM_MSG_KEYRING].retry = MSG_RETRY_COUNT;
      return true;
    } else {
      DPRINTF("Key id not found.");
    }
  } else {
    DPRINTF("Error parsing key.");
  }
  return false;
}


#ifdef ENABLE_WEB_GUI


void set_ringtone(const char *ringtone) {
  static Ticker ticker;
  strcpy(settings.ringtone + 1, ringtone);
  saveSettings();
  bell_end();
  bell_begin();
  ticker.once(5, bell_end);
  // audio_streaming_end();
  // audio_streaming_begin(settings.ringtone);
}

char* settings_json() {
  char *response;
  
  const size_t capacity = JSON_ARRAY_SIZE(32) + 32*JSON_OBJECT_SIZE(2) + JSON_OBJECT_SIZE(3);
  DynamicJsonDocument doc(capacity);

  doc["ringtone"] = settings.ringtone + 1;
  doc["unknown_key"] = unknown_key;

  JsonArray keys = doc.createNestedArray("keys");
  for (int i = 0; i < settings.nkeys; i++) {
    JsonObject key = keys.createNestedObject();
    char string_id[] = "FF:FF:FF:FF";
    uint8_t *id = settings.keys[i].id;
    sprintf(string_id, "%X:%X:%X:%X", id[0], id[1], id[2], id[3]);
    key["guid"] = string_id;
    key["comment"] = settings.keys[i].comment;
  }

  size_t outputSize = measureJson(doc) + 1;
  
  response = new char[outputSize];

  serializeJson(doc, response, outputSize);

  DPRINTF("heap: %d", ESP.getFreeHeap());
  
  return response;
}

#endif

#ifndef DISABLE_STA

void mqtt_callback(const char topic[], byte* payload, unsigned int length) {
  char
    *msg = new char[length + 1],
    *topic_suffix = (char *)topic + strlen("yard/gates/");
  strncpy(msg, (char *)payload, length);
  msg[length] = 0;
  uint8_t id[4];
  int id_int[4];
  
  DPRINTF("Topic: %s, suffix: %s, payload: %s", topic, topic_suffix, msg);
  
  int command;
  for (command = 0; command < MQTT_CMD_UNKNOWN; command++) {
    if (strcmp(topic_suffix, mqtt_command[command]) == 0) {
      break;
    }
  }

  switch (command) {
    case MQTT_CMD_LOCK:
      if (strcmp(msg, "UNLOCK") == 0) {
	if (outgoing_msgs[INTERCOM_MSG_UNLOCK].retry == 0) {
	  outgoing_msgs[INTERCOM_MSG_UNLOCK].retry = MSG_RETRY_COUNT;
	}
      }
      break;

    case MQTT_CMD_KEYS_ADD:
      add_key(msg);
      break;

    case MQTT_CMD_KEYS_DELETE:
      delete_key(msg);
      break;

    case MQTT_CMD_KEYS_LIST:
      char header[] = "### Access keys\n",
	line[50] = "";
      size_t plength = strlen(header);

      for (int i = 0; i < settings.nkeys; i++) {
	uint8_t *id = settings.keys[i].id;
	plength += sprintf(line, "%X:%X:%X:%X;%s\n", id[0], id[1], id[2], id[3], settings.keys[i].comment);
      }

      mqtt.beginPublish("yard/gates/status", plength, false);
      mqtt.print(header);
      for (int i = 0; i < settings.nkeys; i++) {
	uint8_t *id = settings.keys[i].id;
	mqtt.printf("%X:%X:%X:%X;%s\n", id[0], id[1], id[2], id[3], settings.keys[i].comment);
      }
      mqtt.endPublish();
      break;
  }

  delete [] msg;
}

#endif

void confirm_msg(IPAddress ip, int msg) {
  udp.beginPacket(ip, CONTROL_PORT);
  udp.write(INTERCOM_MSG_OK);
  udp.write(msg);
  udp.endPacket();
  delay(UDP_SEND_DELAY);
}

void udp_listen_loop() {

  static unsigned long connectionTimeout = 0;

#ifndef DISABLE_STA

  static uint32_t wifiReconnectTimeout = 0;
  
  if (WiFi.status() != WL_CONNECTED) {
    if (millis() - wifiReconnectTimeout > 30000) {
      DPRINTF("WiFi connection lost (status = %d), reconnecting...", WiFi.status());
      WiFi.reconnect();
      wifiReconnectTimeout = millis();
      delay(10);
    }
    status = HANDSET_STATUS_DISCONNECTED;
    return;
  }

#endif
  
  int bytes = udp.parsePacket();
  if (bytes) {
    int msg = udp.read();
    switch (msg) {
      case INTERCOM_MSG_BELL:
	bell_begin();
      	confirm_msg(udp.remoteIP(), msg);
	break;
	
      case INTERCOM_MSG_PING:
	connectionTimeout = millis();
	confirm_msg(udp.remoteIP(), msg);
	if (status == HANDSET_STATUS_DISCONNECTED) {
	  status = HANDSET_STATUS_IDLE;
	  gatecontrol_ip = udp.remoteIP();
	  DPRINTF("Gate control is now connected. IP: %s", gatecontrol_ip.toString().c_str());
	}
	break;

      case INTERCOM_MSG_UNKNOWN_KEY:
	uint8_t id[4];
	udp.read(id, 4);
#ifndef DISABLE_STA
	char status_update[64];
	sprintf(status_update, "### Unknown key\nid: %X:%X:%X:%X", id[0], id[1], id[2], id[3]);
	mqtt.publish("yard/gates/status", status_update, false);
#endif
#ifdef ENABLE_WEB_GUI
	sprintf(unknown_key, "%X:%X:%X:%X", id[0], id[1], id[2], id[3]);
	broadcastSettings();
#endif
	confirm_msg(udp.remoteIP(), msg);
	break;

      case INTERCOM_MSG_OK:
	int msg_ok = udp.read();
	switch (msg_ok) {
	case INTERCOM_MSG_PING:
	  break;
	  
	case INTERCOM_MSG_UNLOCK:
	  
#ifndef DISABLE_STA
	  mqtt.publish("yard/gates/lock/status", "UNLOCK");
	  mqtt_unlock_published = millis();
#endif
	  // TODO process unlock with some confirmation sound or whatever
	  break;
	  
	case INTERCOM_MSG_HANGUP:
	  // TODO process hangup
	  break;
	  
	case INTERCOM_MSG_CONNECT:
	  // TODO start voice
	  break;
	}
	outgoing_msgs[msg_ok].retry = 0;
	outgoing_msgs[msg_ok].repeat_timeout = 0;
	break;
    }
    connectionTimeout = millis();

  }

#ifndef AUDIO_DEBUG
  // connection timeout
  if (status != HANDSET_STATUS_DISCONNECTED && (millis() - connectionTimeout > 5000)) {
    status = HANDSET_STATUS_DISCONNECTED;
    DPRINTF("Gate control disconnected.");
  }
#endif

  for (int omsg = 0; omsg < INTERCOM_MSG_NUM; omsg++) {
    if (outgoing_msgs[omsg].retry && (outgoing_msgs[omsg].repeat_timeout == 0 || millis() - outgoing_msgs[omsg].repeat_timeout > MSG_RETRY_PERIOD)) {
      udp.beginPacket(gatecontrol_ip, CONTROL_PORT);
      udp.write(omsg);
      if (omsg == INTERCOM_MSG_CONNECT) {
	udp.write(handset_ip[0]);
	udp.write(handset_ip[1]);
	udp.write(handset_ip[2]);
	udp.write(handset_ip[3]);
      } else if (omsg == INTERCOM_MSG_KEYRING) {
	udp.write(settings.nkeys);
	for (int i = 0; i < settings.nkeys; i++) {
	  udp.write(settings.keys[i].id, 4);
	}
      }
      udp.endPacket();
      delay(UDP_SEND_DELAY);
      if (--outgoing_msgs[omsg].retry == 0) {
	outgoing_msgs[omsg].repeat_timeout = 0;
      } else {
	outgoing_msgs[omsg].repeat_timeout = millis();
      }
    }
  }

}


void setup() {

#ifdef DEBUG
  Serial.begin(115200);
  Serial.println("HOUSTON IS READY");
#endif

  if (!SPIFFS.begin()) {
    DPRINTF("SPIFFS.begin() failed");
    // return;
  } else {
    readSettings();
  }

  
#ifndef DISABLE_STA  
  WiFiManager wifiManager;
  // WifiManager.resetSettings(); // reset saved SSID and password

#ifndef DEBUG
  wifiManager.setDebugOutput(false);
#endif

  wifiManager.setTimeout(300);  
  if (!wifiManager.autoConnect(houston_ap_ssid, houston_ap_psk)) {
    DPRINTF("Failed to connect to AP...");
  }
  
  WiFi.mode(WIFI_AP_STA);
#else
  WiFi.mode(WIFI_AP);
#endif

  WiFi.setSleepMode(WIFI_NONE_SLEEP);
  WiFi.setAutoConnect(false);
  WiFi.setAutoReconnect(false);
  WiFi.softAPConfig(IPAddress(HOUSTON_IP), IPAddress(HOUSTON_IP), IPAddress(255,255,255,0));
  // WiFi.setOutputPower(20.5);
  WiFi.softAP(houston_ap_ssid, houston_ap_psk, WiFi.channel(), SOFT_AP_HIDDEN);

#ifdef DISABLE_STA
  WiFi.enableAP(true);
  DPRINTF("SSID: %s, PSK: %s", houston_ap_ssid, houston_ap_psk);
#else
  WiFi.reconnect();
  DPRINTF("SSID: %s, PSK: %s", houston_ap_ssid, houston_ap_psk);
#endif
  
  ArduinoOTA.setHostname("houston");
  ArduinoOTA.begin();

#ifndef DISABLE_STA  
  mqtt.setCallback(mqtt_callback);
#endif

#ifdef ENABLE_WEB_GUI
  setupWebUI();
#endif

  udp.begin(CONTROL_PORT);

  for (int i = 0; i < INTERCOM_MSG_NUM; i++) {
    outgoing_msgs[i].retry = 0;
    outgoing_msgs[i].repeat_timeout = 0;
  }

  SPI.begin();
  
  audio_init();

  pinMode(CONNECT_BTN_PIN, INPUT_PULLUP);
  pinMode(UNLOCK_BTN_PIN, INPUT_PULLUP);
  digitalWrite(SPK_EN_PIN, !SPK_EN);
  pinMode(SPK_EN_PIN, OUTPUT);

  pinMode(LED_DATA_PIN, OUTPUT);

  leds.begin();

  audio_streaming_begin("/success.g722");

}

void loop() {

  static unsigned long conn_btn_debounce = 0, unlock_btn_debounce;
  static bool conn_btn_state = !CONNECT_BTN_ACTIVE, last_conn_btn_state = !CONNECT_BTN_ACTIVE,
    unlock_btn_state = HIGH, last_unlock_btn_state = HIGH;

  static int btn_down_status;
  
  bool reading = digitalRead(CONNECT_BTN_PIN);
  
  if (reading != last_conn_btn_state) {
    conn_btn_debounce = millis();
    last_conn_btn_state = reading;
  }
  
  if (reading != conn_btn_state && millis() - conn_btn_debounce > 50) {
    conn_btn_state = reading;
    if (conn_btn_state == CONNECT_BTN_ACTIVE) {
      // connect/hangup button pressed
      if (status == HANDSET_STATUS_DISCONNECTED) { // no connection to gatecontrol unit
	bell_end();
	audio_streaming_begin("/error.g722");
      } else if (status != HANDSET_STATUS_VOICE && status != HANDSET_STATUS_VOICE_MUTE) { // voice already in progress
	handset_ip = WiFi.softAPIP();
	outgoing_msgs[INTERCOM_MSG_CONNECT].retry = MSG_RETRY_COUNT;
	voice_begin();
      }
    } else {
      // connect/hangup button released
      if (status == HANDSET_STATUS_VOICE || status == HANDSET_STATUS_VOICE_MUTE) { // hangup
	voice_end();
	outgoing_msgs[INTERCOM_MSG_HANGUP].retry = MSG_RETRY_COUNT;
      }
    }
  }

  reading = digitalRead(UNLOCK_BTN_PIN);
  if (reading != last_unlock_btn_state) {
    unlock_btn_debounce = millis();
    last_unlock_btn_state = reading;
  }

  if (reading != unlock_btn_state && millis() - unlock_btn_debounce > 50) {
    unlock_btn_state = reading;
    if (unlock_btn_state == LOW) {
      if (status == HANDSET_STATUS_RINGING) {
	bell_end();
      }
      if (status == HANDSET_STATUS_DISCONNECTED) {
	audio_streaming_begin("/error.g722");
      } else {
	outgoing_msgs[INTERCOM_MSG_UNLOCK].retry = MSG_RETRY_COUNT;
      }
    }
  }

  // voice communication timeout or disconnect
  if (voice_started && (status == HANDSET_STATUS_DISCONNECTED || millis() - voice_started >= VOICE_TIME_LIMIT)) {
    DPRINTF("Voice connection time out or UDP connection lost.");
    voice_end();
  }

  // ringer timeout or disconnect
  if (ringer_started && (status != HANDSET_STATUS_RINGING || millis() - ringer_started >= 30000)) {
    bell_end();
  }

  if (status == HANDSET_STATUS_RINGING && (ringer_repeat_timeout == 0 || millis() - ringer_repeat_timeout >= 5000)) {
    audio_streaming_begin(settings.ringtone);
    ringer_repeat_timeout = millis();
  }
  
  // Handle OTA if we dont do anything time critical
  if (!audio_sampling() && !audio_playing()) { 
    ArduinoOTA.handle();
  }

#ifdef ENABLE_WEB_GUI
  if (!audio_sampling()) {
    loopWebUI();
  }
#endif


#ifndef DISABLE_STA
  // poll mqtt every once in a while as it's quite slow
  static unsigned long mqttLastLoop = 0;
  if (millis() - mqttLastLoop >= 400) {
    mqttLastLoop = millis();
    if (!mqtt.loop()) {
      mqtt_reconnect();
    } else {
      if (mqtt_unlock_published && millis() - mqtt_unlock_published > 10000) {
	mqtt.publish("yard/gates/lock/status", "LOCK");
	mqtt_unlock_published = 0;
      }
    }
  }
#endif
  
  static int previous_status = HANDSET_STATUS_NONE;
  static unsigned long status_led_update_timeout = 0;
  static bool blink;
  if (status == HANDSET_STATUS_IDLE || previous_status != status || millis() - status_led_update_timeout >= 1000) {
    previous_status = status;
    status_led_update_timeout = millis();
    uint32_t ledColor;
    if (status == HANDSET_STATUS_IDLE) {
      ledColor = leds.Color(0, map(leds.sine8(millis() >> 4), 0, 255, 1, 12), 0);
    } else {
      blink = !blink;
      ledColor = (status == HANDSET_STATUS_RINGING && blink) ? 0 : status_color[status];
    }
    leds.setPixelColor(0, ledColor);
    leds.show();
  }

  udp_listen_loop();
  audio_buffer_loop();
  delay(1);
}

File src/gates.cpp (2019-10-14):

#include <Arduino.h>

#include <SPI.h>

#define MFRC522_SPICLOCK SPI_CLOCK_DIV4
#include <MFRC522.h>

#include <WiFiManager.h>
#include <ArduinoOTA.h>
#include <FS.h>

#include "doorphone.h"
#include "audio.h"

WiFiUDP udp;

#define ADC_CS 15
#define MFRC_RST_PIN      4  // Configurable, see typical pin layout above
#define MFRC_SS_PIN       16 // Configurable, see typical pin layout above
#define LOCK_CONTROL_PIN  5

// #define MFRC_MAX_GAIN

unsigned long voice_started = 0,
  unlockPulseTimeout = 0;

bool connected = false;
bool card_reader_is_shutdown = false;

IPAddress houston_ip = IPAddress(HOUSTON_IP);

uint8_t keys[32][4];
uint8_t nkeys = 0;
uint8_t unknown_key[4];

static struct {
  int retry;
  int repeat_timeout;
} outgoing_msgs[INTERCOM_MSG_NUM];

MFRC522 mfrc522(MFRC_SS_PIN, MFRC_RST_PIN);  // Create MFRC522 instance

void card_reader_init() {
  DPRINTF("MFRC522_SPICLOCK = %d, SPI_CLOCK_DIV16 = %d", MFRC522_SPICLOCK, SPI_CLOCK_DIV16);

  pinMode(MFRC_RST_PIN, INPUT_PULLUP);
  
  if (digitalRead(MFRC_RST_PIN) == HIGH) {
    mfrc522.PCD_Init();

#ifdef MFRC_MAX_GAIN
    mfrc522.PCD_AntennaOff();
    mfrc522.PCD_SetAntennaGain(MFRC522::RxGain_max); // RxGain_38dB RxGain_43dB RxGain_max
    mfrc522.PCD_AntennaOn();
#endif
    pinMode(MFRC_RST_PIN, INPUT_PULLUP);
  }

}

void card_reader_shutdown() {
  pinMode(MFRC_RST_PIN, OUTPUT);
  digitalWrite(MFRC_RST_PIN, LOW); // turn off RFID reader, it messes up MISO
}

void audio_play(const char *filename) {
  card_reader_shutdown();
  card_reader_is_shutdown = true;
  audio_streaming_begin(filename);
}


int key_index(uint8_t id[4]) {
  for (int i = 0; i < nkeys; i++) {
    if (memcmp(keys[i], id, 4) == 0)
      return i;
  }
  return -1;
}

void load_keys() {
  File f = SPIFFS.open("keyring.dat", "r");
  if (!f) {
    DPRINTF("Can't open keyring file.");
    return;
  }

  nkeys = f.read();
  f.read(keys[0], nkeys*4);
  f.close();

  DPRINTF("Keys in keyring: %d", nkeys);
  for (int i = 0; i<nkeys; i++) {
    DPRINTF("Key #%d: %X:%X:%X:%X", i, keys[i][0], keys[i][1], keys[i][2], keys[i][3]);
  }
}

void save_keys() {
  File f = SPIFFS.open("keyring.dat", "w");
  if (!f) {
    DPRINTF("Can't open keyring file.");
    return;
  }

  f.write(nkeys);
  f.write(keys[0], nkeys*4);
  f.close();

  DPRINTF("Keys saved.");
}


void doorUnlock() {

  digitalWrite(LOCK_CONTROL_PIN, LOW);
  unlockPulseTimeout = millis();

#ifdef UNIT16  
  audio_play("/success.g722");
#else
  audio_play("/success.low.g722");
#endif
}

void voice_begin(IPAddress handset_ip) {

  card_reader_shutdown();

  audio_streaming_end(); // in case bell sound is still playing
  audio_streaming_begin(UDPSTREAM);
  audio_sampling_begin(handset_ip);
  voice_started = millis();

  DPRINTF("Starting voice communication to %s", handset_ip.toString().c_str());
  
}


void voice_end() {
  audio_sampling_end();
  audio_streaming_end();
  card_reader_init();
  voice_started = 0;
  DPRINTF("Voice communication ended.");
}

void confirm_msg(IPAddress ip, int msg) {
  udp.beginPacket(ip, CONTROL_PORT);
  udp.write(INTERCOM_MSG_OK);
  udp.write(msg);
  udp.endPacket();
  delay(UDP_SEND_DELAY);
}

void card_scan_loop() {

  // make sure we don't touch SPI while sampling audio with SPI ADC  
  if (audio_sampling() || audio_playing()) {
    return;
  }

  if (!mfrc522.PICC_IsNewCardPresent() || !mfrc522.PICC_ReadCardSerial()) {
    return;
  }

#ifdef DEBUG
  // Dump debug info about the card; PICC_HaltA() is automatically called
  mfrc522.PICC_DumpToSerial(&(mfrc522.uid));
#endif
  
  uint8_t readCard[4];

  DPRINTF("Card serial bytes:");
  for ( uint8_t i = 0; i < mfrc522.uid.size; i++) {
    DPRINTF("%X", mfrc522.uid.uidByte[i]);
    readCard[i] = mfrc522.uid.uidByte[i];
  }

  mfrc522.PICC_HaltA();
  mfrc522.PCD_StopCrypto1();

  if (key_index(readCard) != -1) { // check if known card 
    doorUnlock();
    // a little hack to trigger mqtt lock status via handset unit
    confirm_msg(houston_ip, INTERCOM_MSG_UNLOCK);
  } else {
    // queue unknown key message
    memcpy(unknown_key, readCard, 4);
    outgoing_msgs[INTERCOM_MSG_UNKNOWN_KEY].retry = MSG_RETRY_COUNT;
#ifdef UNIT16
    audio_play("/error.g722");
#else
    audio_play("/error.low.g722");
#endif
  }
}

void udp_listen_loop() {

  static unsigned long connectionTimeout = 0;
  static unsigned long doorbellRepeatTimeout = 0;
  static unsigned long wifiReconnectTimeout = 0;
  static unsigned long ping_timeout = 0;
  
  if (WiFi.status() != WL_CONNECTED) {
    if (millis() - wifiReconnectTimeout > 5000) {
      DPRINTF("WiFi connection lost (status = %d), reconnecting...", WiFi.status());
      // WiFi.disconnect();
      // WiFi.begin(houston_ap_ssid, houston_ap_psk);
      // // WiFi.reconnect();
      wifiReconnectTimeout = millis();
      // delay(10);
    }
    connected = false;
    return;
  } else {
    houston_ip = WiFi.gatewayIP();
  }
  
  int bytes = udp.parsePacket();
  if (bytes) {
    int msg = udp.read();
    switch (msg) {
      case INTERCOM_MSG_UNLOCK:
	doorUnlock();
	confirm_msg(udp.remoteIP(), msg);
	break;
	
      case INTERCOM_MSG_CONNECT:
	uint8_t address[4];
	if (udp.read(address, 4) == 4) {
	  voice_begin(IPAddress(address));
	  confirm_msg(udp.remoteIP(), msg);
	}
	break;
	
      case INTERCOM_MSG_HANGUP:
	voice_end();
	confirm_msg(udp.remoteIP(), msg);
	break;

      case INTERCOM_MSG_KEYRING:
	nkeys = udp.read();
	if (nkeys <= 32) {
	  udp.read(keys[0], nkeys*4);
	  save_keys();
	} else {
	  DPRINTF("Error saving keyring: too many keys received.");
	}
	confirm_msg(udp.remoteIP(), msg);
	break;

      case INTERCOM_MSG_OK:
	int msg_ok = udp.read();
	if (msg_ok == INTERCOM_MSG_PING) {
	  connectionTimeout = millis();
	  if (!connected) {
	    connected = true;
	    DPRINTF("UDP connection established.");
	  }
	}
	outgoing_msgs[msg_ok].retry = 0;
	outgoing_msgs[msg_ok].repeat_timeout = 0;
	break;
    }
    connectionTimeout = millis();
    if (!connected) {
      connected = true;
      DPRINTF("UDP connection established.");
    }
  }

  // connection timeout
  if (connected && (millis() - connectionTimeout > 5000)) {
    connected = false;
    DPRINTF("UDP connection lost.");
  }

  // ping houston module every second
  if (millis() - ping_timeout >= 1000) {
    udp.beginPacket(houston_ip, CONTROL_PORT);
    udp.write(INTERCOM_MSG_PING);
    if (!udp.endPacket()) {
      DPRINTF("udp.endPacket() error.");
    }
    delay(UDP_SEND_DELAY);
    ping_timeout = millis();
  }
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

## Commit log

2019-01-18 Reduce actuator stall current peaks
    [lock.cpp]
2019-10-14 Switch ISR to timer 0, SPI transaction
2019-10-14 Small fixes, option for another unit
    [gates.cpp]
2019-10-14 v1 schematics and PCBs
    [gates-v1-speaker.kicad_pcb, gates-v1-speaker.sch, gates-v1.kicad_pcb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]
2019-10-15 OpenSCAD models
    [handset.scad, junction-boxes.scad, speaker-unit.scad]
